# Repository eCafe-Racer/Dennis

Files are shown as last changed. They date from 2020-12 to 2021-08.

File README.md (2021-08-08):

# Dennis

Dennis is a part of the eCafe Racer project, a collaboration between Tim
LaGreca, Jordyn Brosemer, and Connor Winiarczyk where we are attempting to
build an electric racing motorcycle for fun and street cred.

The board serve's as both a controller for the bike's 12V digital signals
(such as its turn signals and brake lights), and also as a general interface
to the bike's CAN bus. We plan to use this interface both during development
for things like data acquisition and validation testing, as well as in the 
final product in order to provide features like control over bluetooth and
diagnostics.

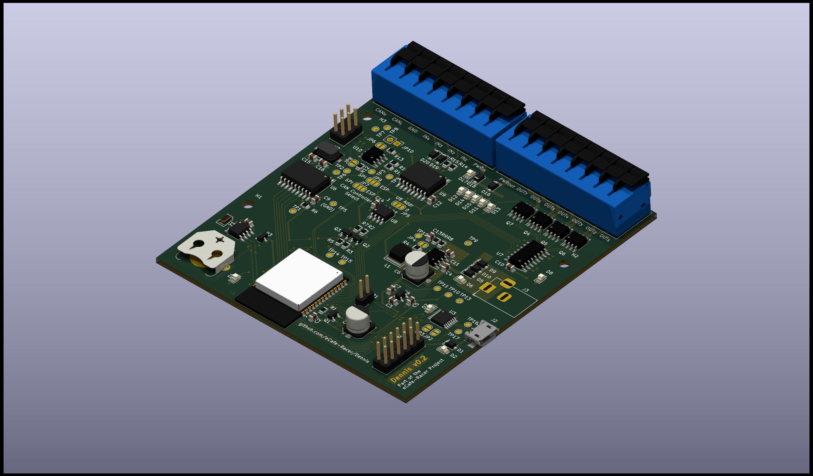
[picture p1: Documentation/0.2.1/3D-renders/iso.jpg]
Isometric View


## Design 

Dennis was originally designed as a carrier board for the Raspberry Pi
[Compute Module 4](https://www.raspberrypi.org/products/compute-module-4/?variant=raspberry-pi-cm4001000),
which aimed to integrate a complete embedded Linux system with the rest of the
circuitry, with peripherals controlled directly by the Pi's GPIO pins.
There were a number of issues with this approach, not the least of which was
that, as hobbyists, we lacked the equipment required to reliably solder the
CM4's high density connectors. There were some more subtle issues as well,
including that the high level of integration made our design much more
difficult to modify, and that the need to include integrated communication
interfaces for the pi increased both the size of the board and its complexity.

Our solution was simply to remove the Compute Module from the design, replacing
it with an ESP32 microcontroller. The microcontroller will be able to perform 
some simple logical control over the board, but its main job will be to provide
an interface to the board's peripherals over UART or USB, allowing a more
powerful computer to connect and perform higher level control and more
sophisticated analysis.  

In order to make interfacing with external computers easier, a 12 pin connector
(J1) was added to Dennis that exactly matches the pinout of the first 12
pins of the 40 pin connector on a traditional Raspberry Pi board. This allows
a Raspberry Pi to be mounted adjacent to Dennis in whatever enclosure it is 
being used in, and with a single ribbon cable, connect to the ESP's UART
interface, as well as the strapping pins needed to do firmware updates, the
board's I2C bus, and 5V power supply. These signals can also be controlled
over USB by way of an MCP2221A, giving us the flexibility to use other external
computers as well.

## Peripherals

Dennis has a 12V GPIO system with 7 digital outputs and 4 digital inputs.
Digital outputs can be set to either 12V (on), or High Impedance (off), meaning
they cannot sink current. The digital inputs consist of two "signal" inputs,
which measure voltage, and two "switch" inputs, which measure resistance to
ground. The switch inputs are meant to make it easier to install switches or
buttons on the bike and to program them for near arbitrary behavior, like
turn signals or a horn.

## Resources

- [Schematic](https://raw.githubusercontent.com/eCafe-Racer/Dennis/master/Documentation/0.2.1/schematic.pdf)
- [Step File](https://raw.githubusercontent.com/eCafe-Racer/Dennis/master/Documentation/0.2.1/step-file.step)
- [Gerbers](https://raw.githubusercontent.com/eCafe-Racer/Dennis/master/production/0.2/gerbers.zip)

- Top View
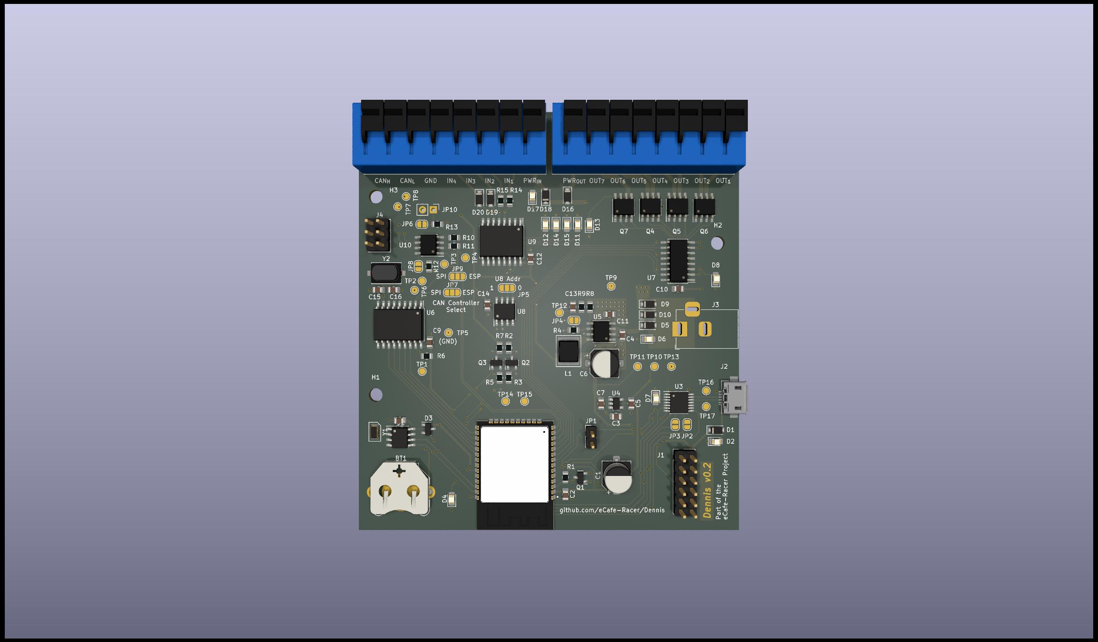
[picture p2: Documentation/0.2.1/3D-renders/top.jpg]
Top View


- Bottom View
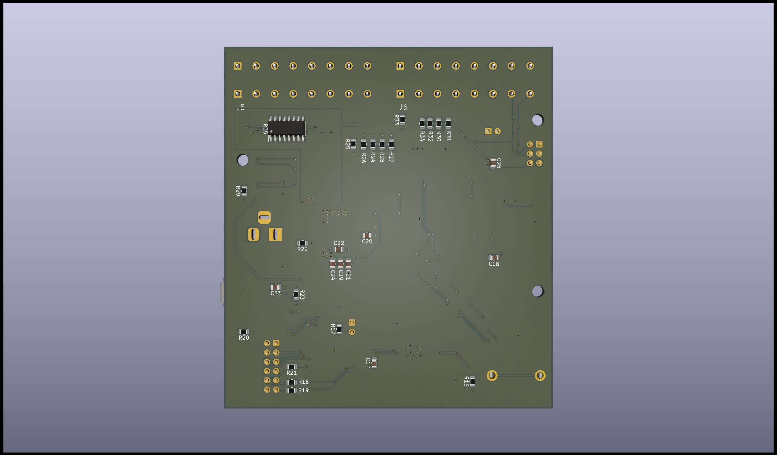
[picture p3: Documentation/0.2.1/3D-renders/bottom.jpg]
Bottom View


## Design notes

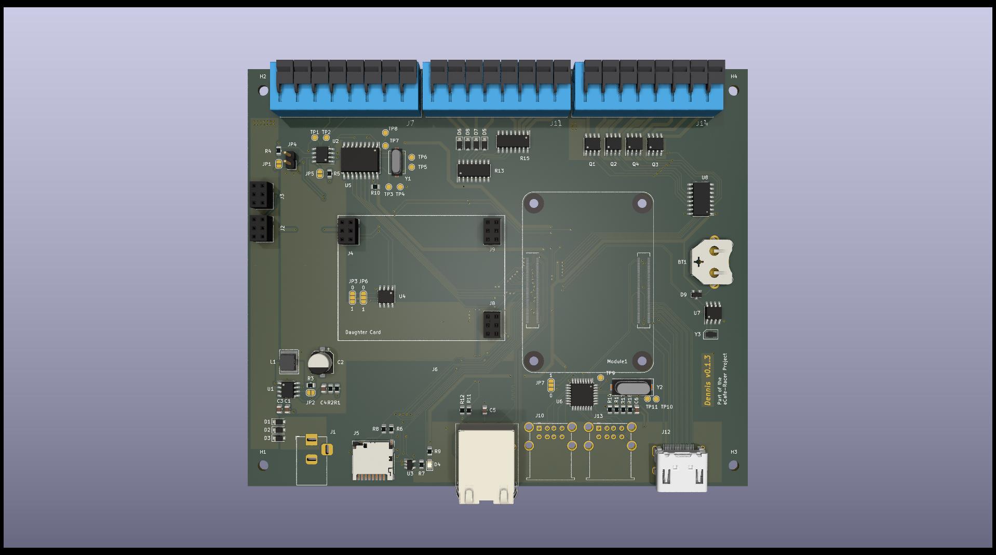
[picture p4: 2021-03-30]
Documentation/0.1.3/images/render_front.jpg

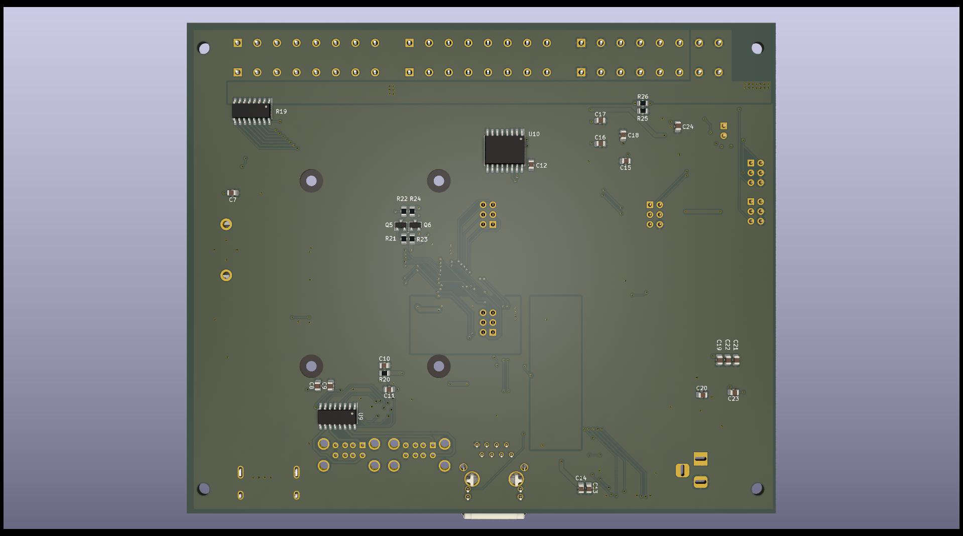
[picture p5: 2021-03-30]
Documentation/0.1.3/images/render_back.jpg

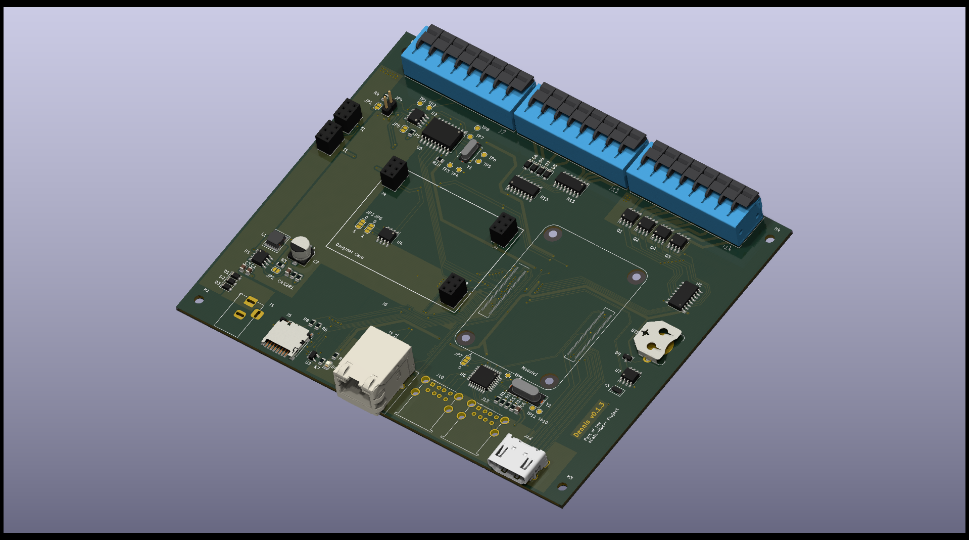
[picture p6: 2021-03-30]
Documentation/0.1.3/images/render_iso.png

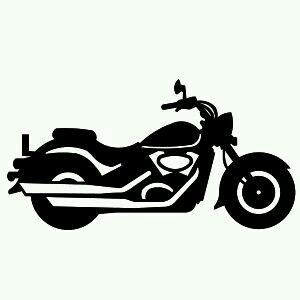
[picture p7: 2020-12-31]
page_layout/cafe-racer-art.jpg

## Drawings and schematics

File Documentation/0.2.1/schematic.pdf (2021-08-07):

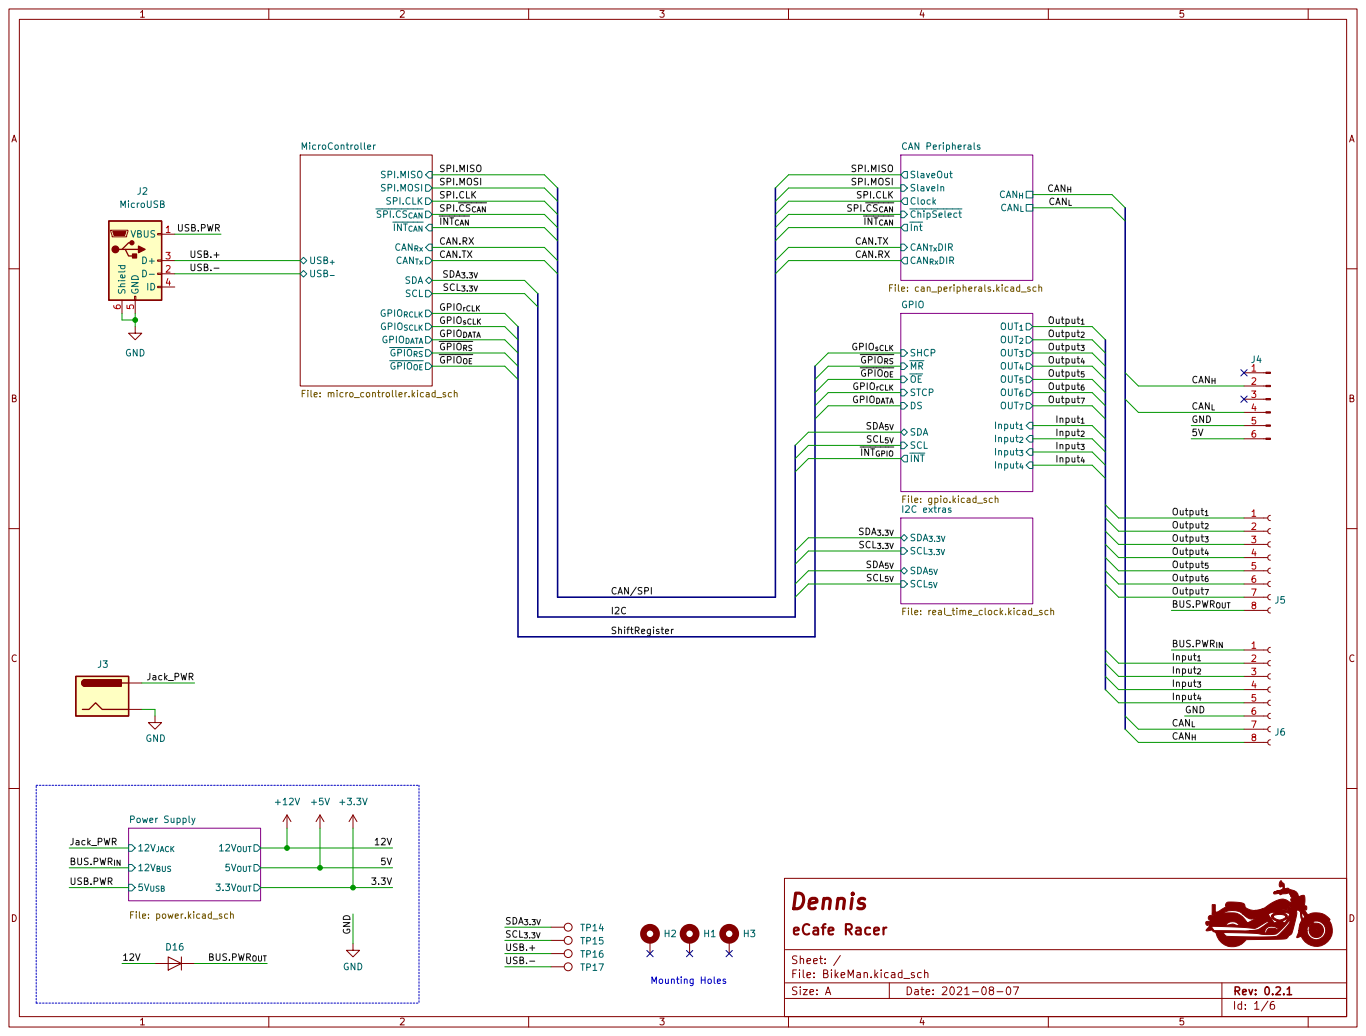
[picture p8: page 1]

MicroController File: micro_controller.kicad_sch SPI.MISO
SCL_{3.3V} SPI.MISO
SPI.MOSI SPI.CLK GPIO_{DATA}
GPIO_{sCLK} USB.+ SCL_{3.3V}
~{GPIO_{RS}} 5V
~{GPIO_{RS}}

SPI.MOSI SPI.MISO

File: can_peripherals.kicad_sch SlaveOut SlaveIn ~{Int}

SPI.MOSI SPI.CLK

SPI.~{CS_{CAN}} CAN.RX CAN.TX GND
~{SPI.CS_{CAN}}
~{INT_{CAN}}
CAN_{Rx}
CAN_{Tx}
~{GPIO_{OE}} SDA

SCL_{3.3V} CAN.RX CAN.TX

BUS.PWR_{IN} USB.PWR

Id: 1/6 Dennis
File: BikeMan.kicad_sch Sheet: / eCafe Racer

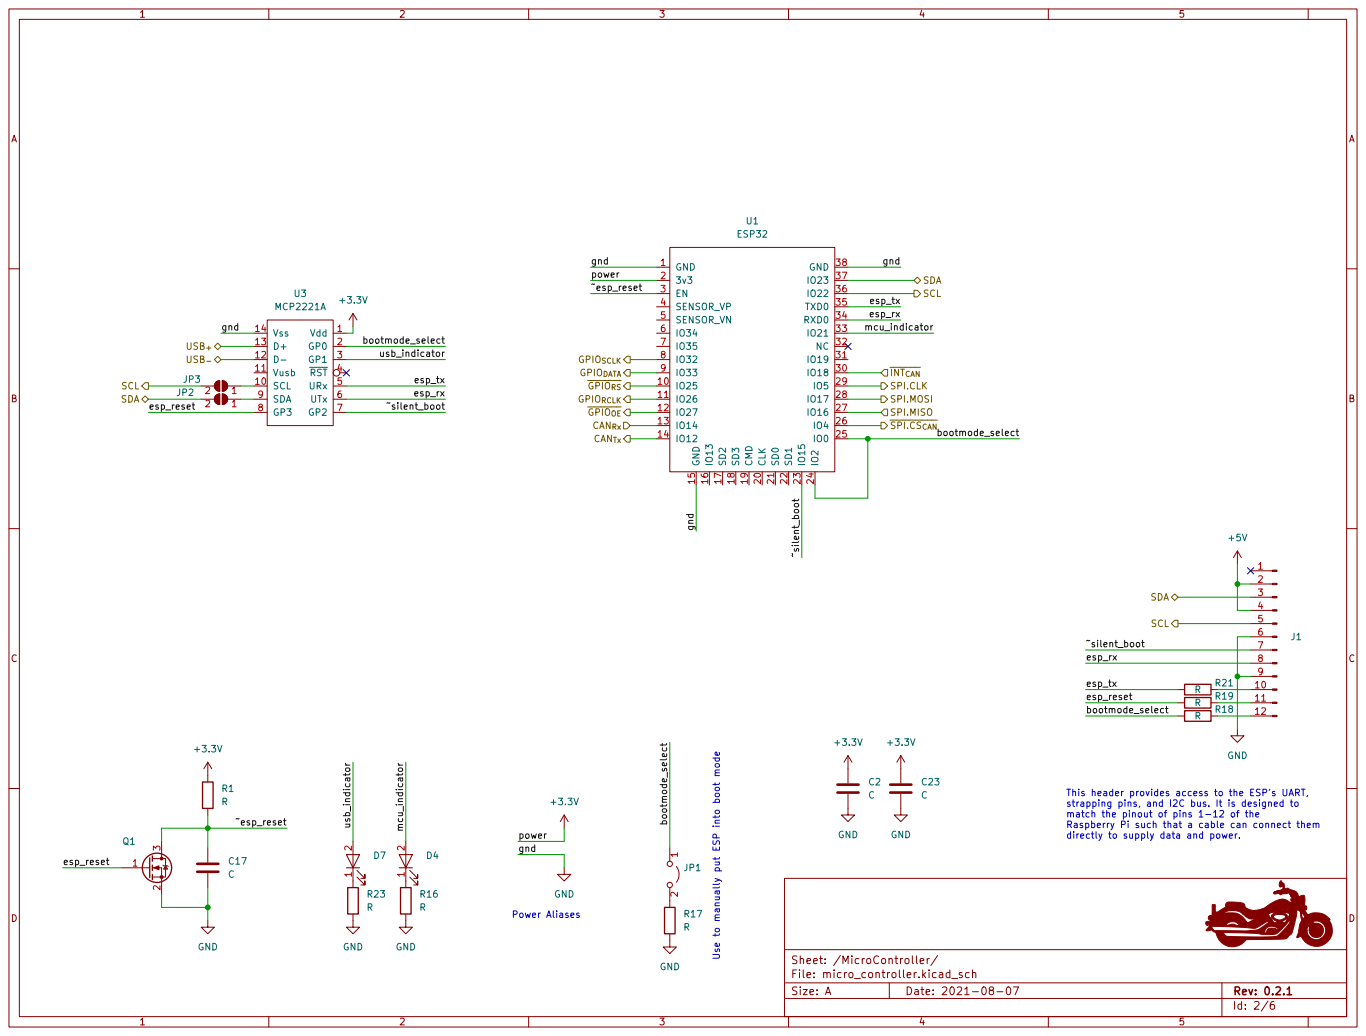
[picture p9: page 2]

strapping pins, and I2C bus. It is designed to
match the pinout of pins 1-12 of the
Raspberry Pi such that a cable can connect them
directly to supply data and power.

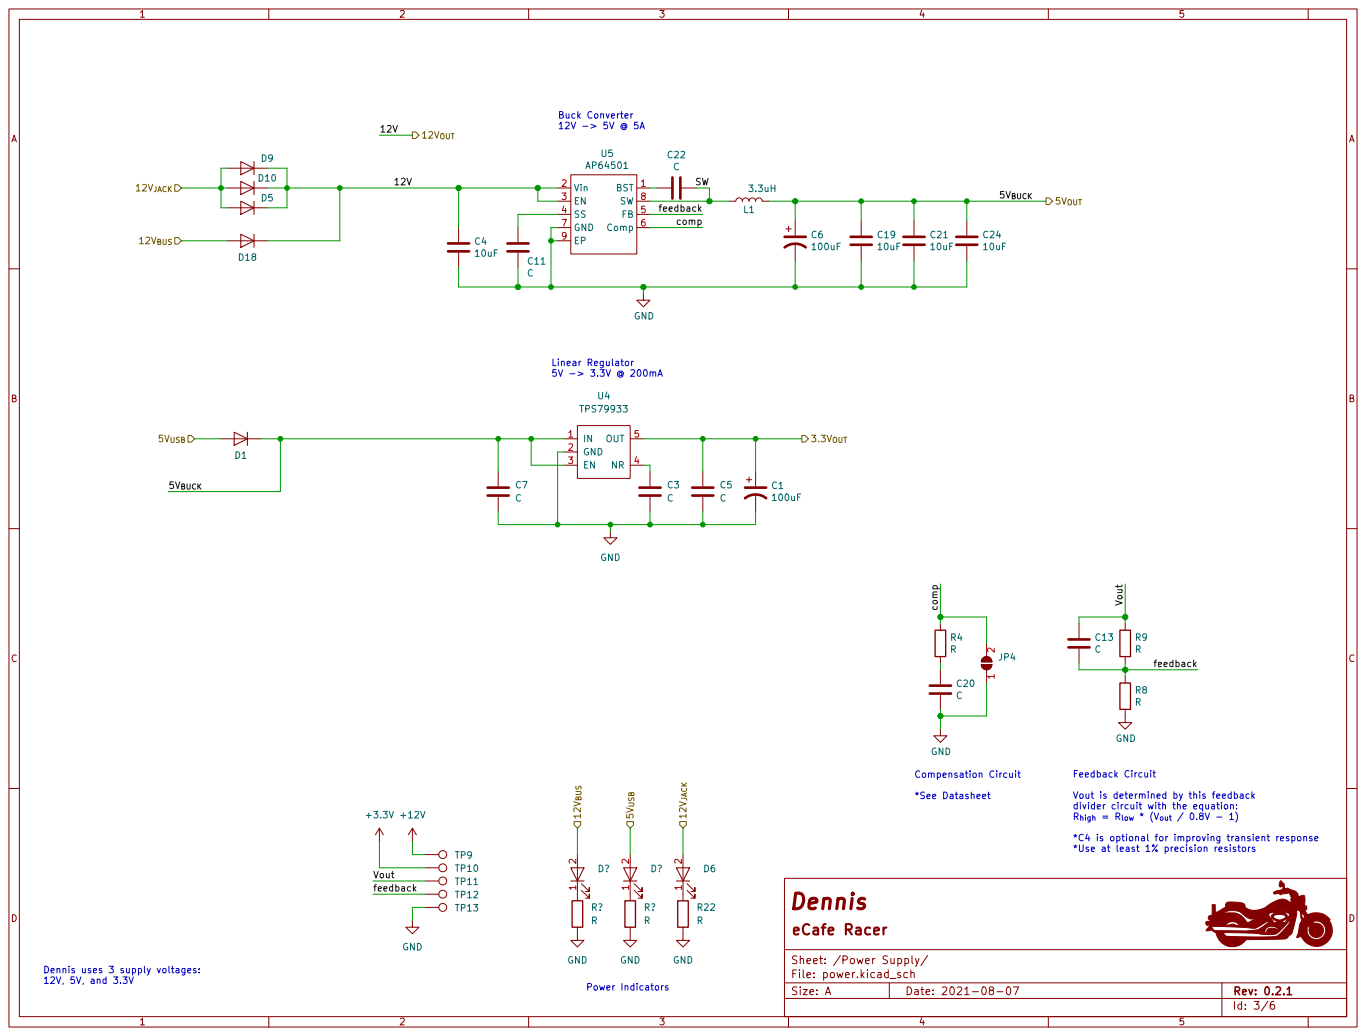
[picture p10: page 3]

Feedback Circuit Vout is determined by this feedback

divider circuit with the equation:
R_{high} = R_{low} * (V_{out} / 0.8V - 1)

*C4 is optional for improving transient response
*Use at least 1% precision resistors

Dennis uses 3 supply voltages: 12V, 5V, and 3.3V

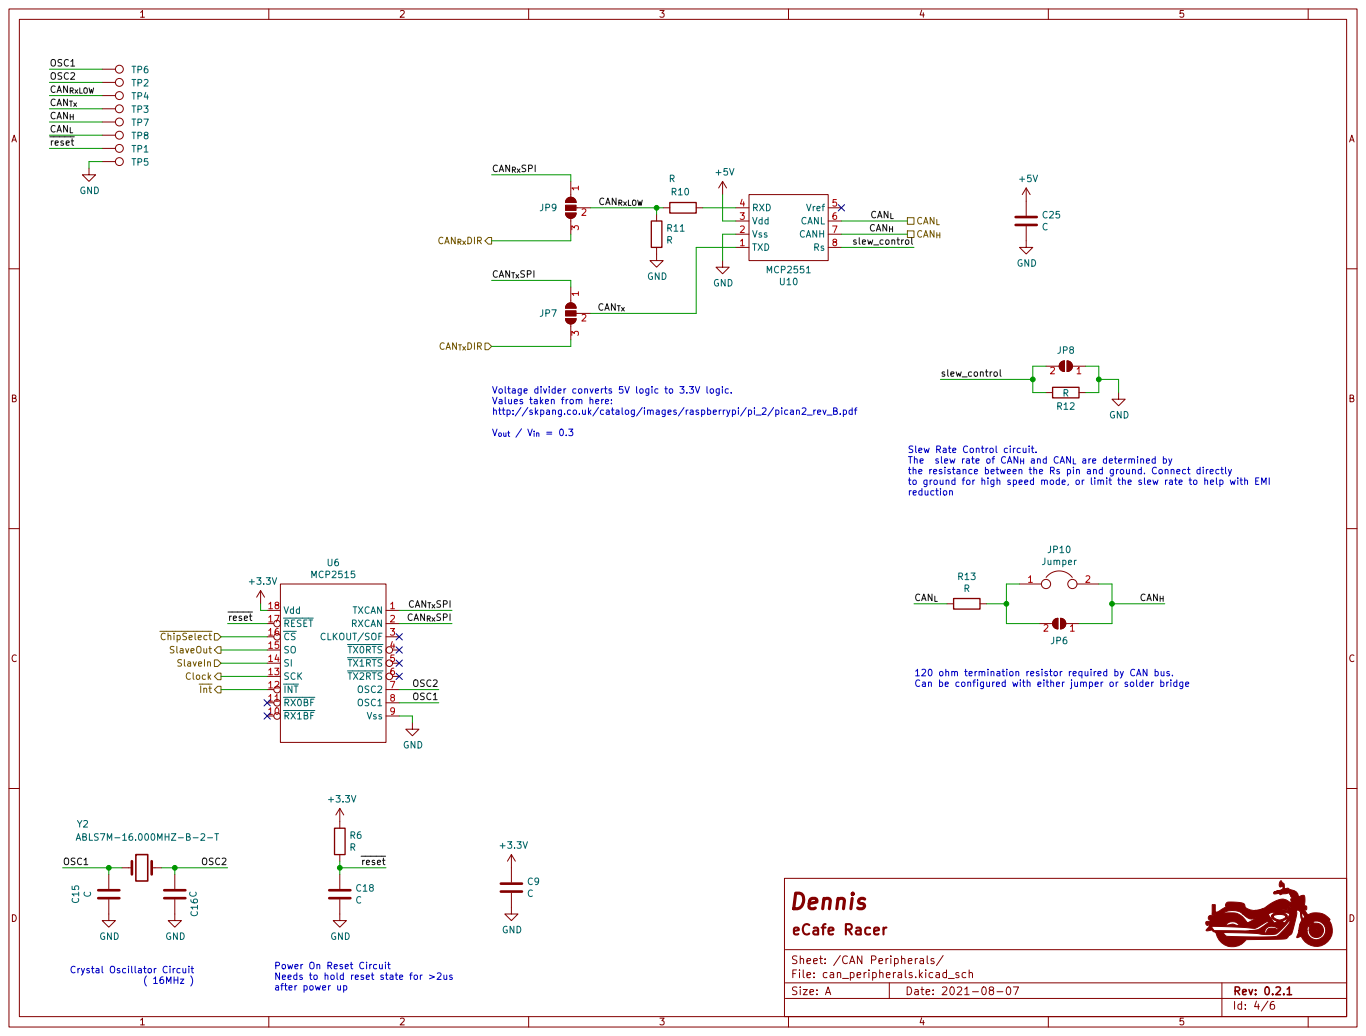
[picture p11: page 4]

Voltage divider converts 5V logic to 3.3V logic. Values taken from here: http://skpang.co.uk/catalog/images/raspberrypi/pi_2/pican2_rev_B.pdf

Slew Rate Control circuit. The slew rate of CAN_{H} and CAN_{L} are determined by

to ground for high speed mode, or limit the slew rate to help with EMI reduction Power On Reset Circuit Needs to hold reset state for >2us after power up

the resistance between the Rs pin and ground. Connect directly

~{ChipSelect}
~{Int} Clock SlaveIn SlaveOut

120 ohm termination resistor required by CAN bus.
Can be configured with either jumper or solder bridge

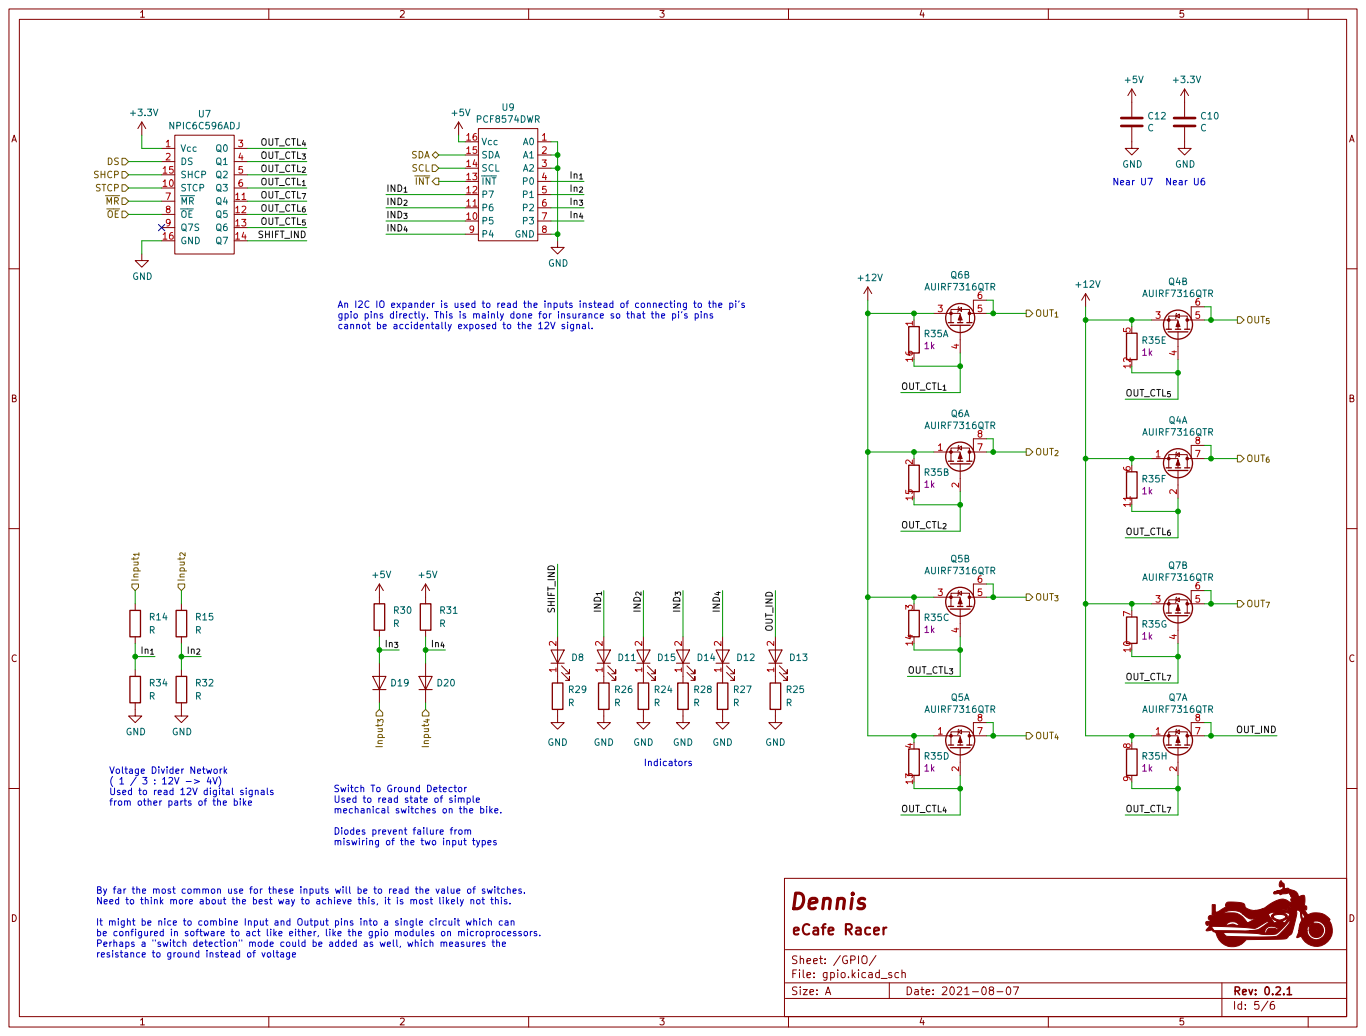
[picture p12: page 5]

1k SCL ~{MR} STCP
Near U7 Voltage Divider Network

An I2C IO expander is used to read the inputs instead of connecting to the pi's
gpio pins directly. This is mainly done for insurance so that the pi's pins

Indicators Switch To Ground Detector Used to read state of simple mechanical switches on the bike. Diodes prevent failure from

Used to read 12V digital signals
from other parts of the bike

miswiring of the two input types

By far the most common use for these inputs will be to read the value of switches.
Need to think more about the best way to achieve this, it is most likely not this.

Id: 5/6 Dennis
File: gpio.kicad_sch Sheet: /GPIO/ eCafe Racer

It might be nice to combine Input and Output pins into a single circuit which can
be configured in software to act like either, like the gpio modules on microprocessors.
Perhaps a "switch detection" mode could be added as well, which measures the
resistance to ground instead of voltage

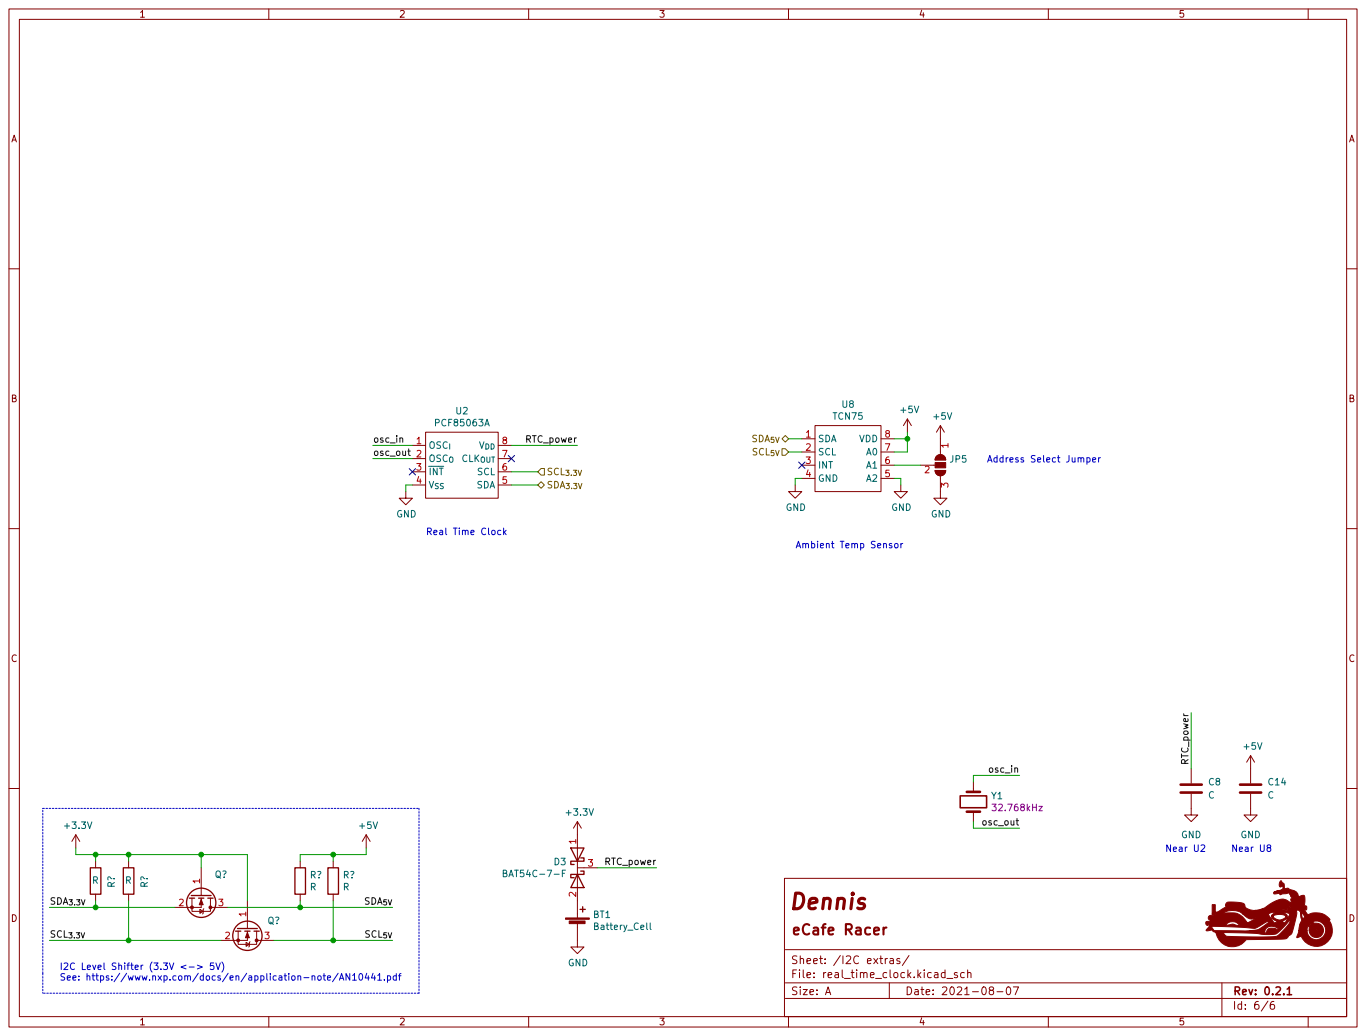
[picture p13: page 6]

File: real_time_clock.kicad_sch Sheet: /I2C extras/ eCafe Racer GND

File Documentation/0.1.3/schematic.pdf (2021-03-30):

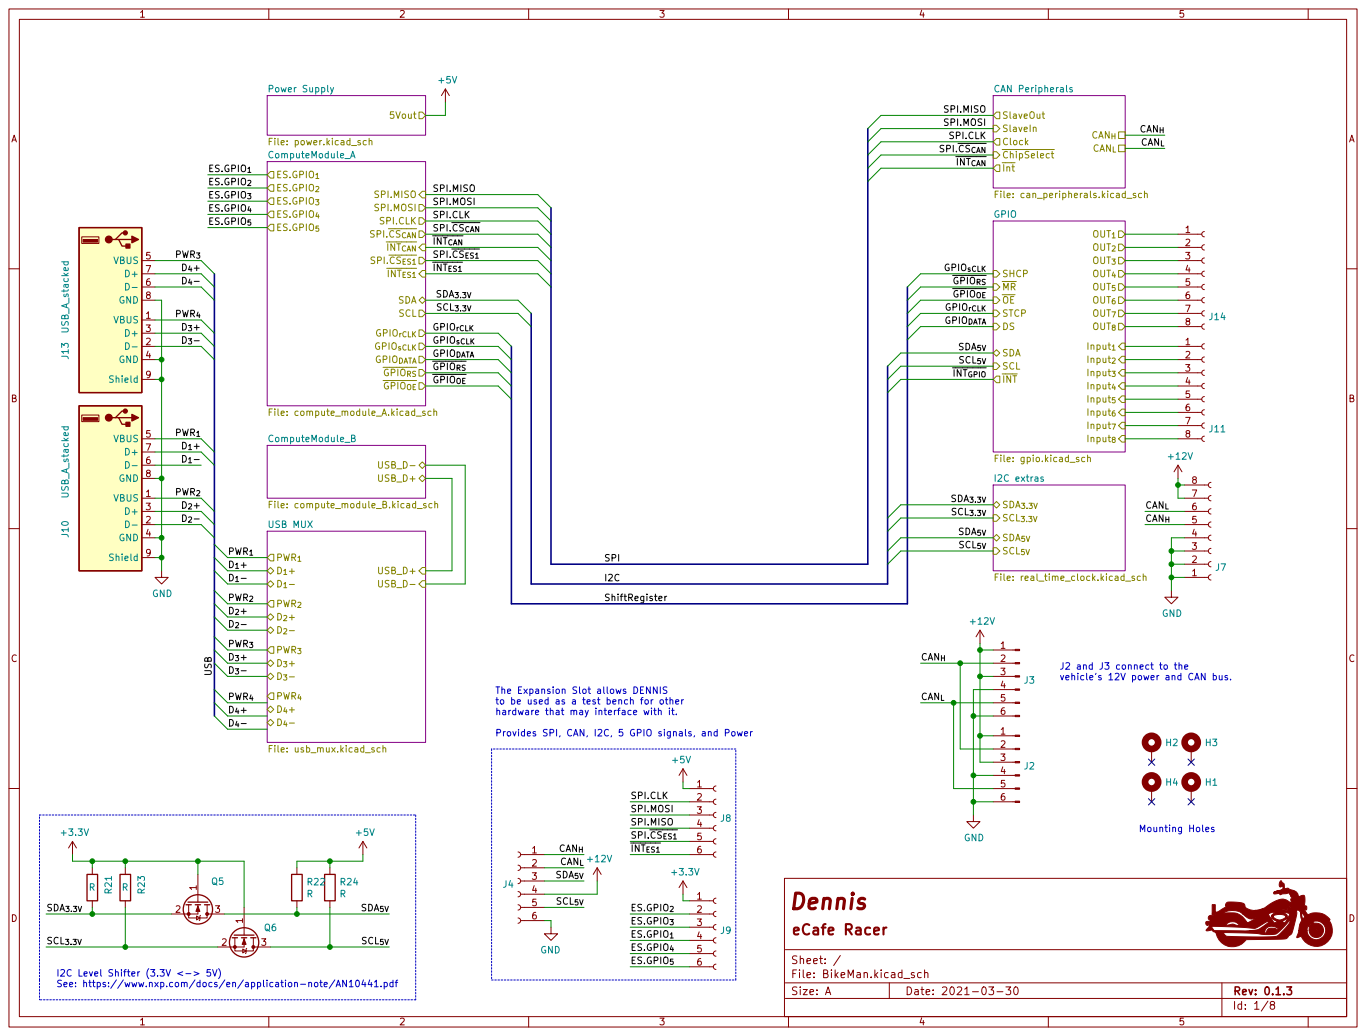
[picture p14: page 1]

SPI.MOSI SPI.MISO

SPI.~CS_{CAN} SPI.MISO
SPI.MOSI SPI.CLK

File: BikeMan.kicad_sch Sheet: / eCafe Racer USB MUX

SPI.MOSI ShiftRegister SPI

vehicle's 12V power and CAN bus.

The Expansion Slot allows DENNIS
to be used as a test bench for other hardware that may interface with it.

Provides SPI, CAN, I2C, 5 GPIO signals, and Power

I2C Level Shifter (3.3V <-> 5V)
See: https://www.nxp.com/docs/en/application-note/AN10441.pdf

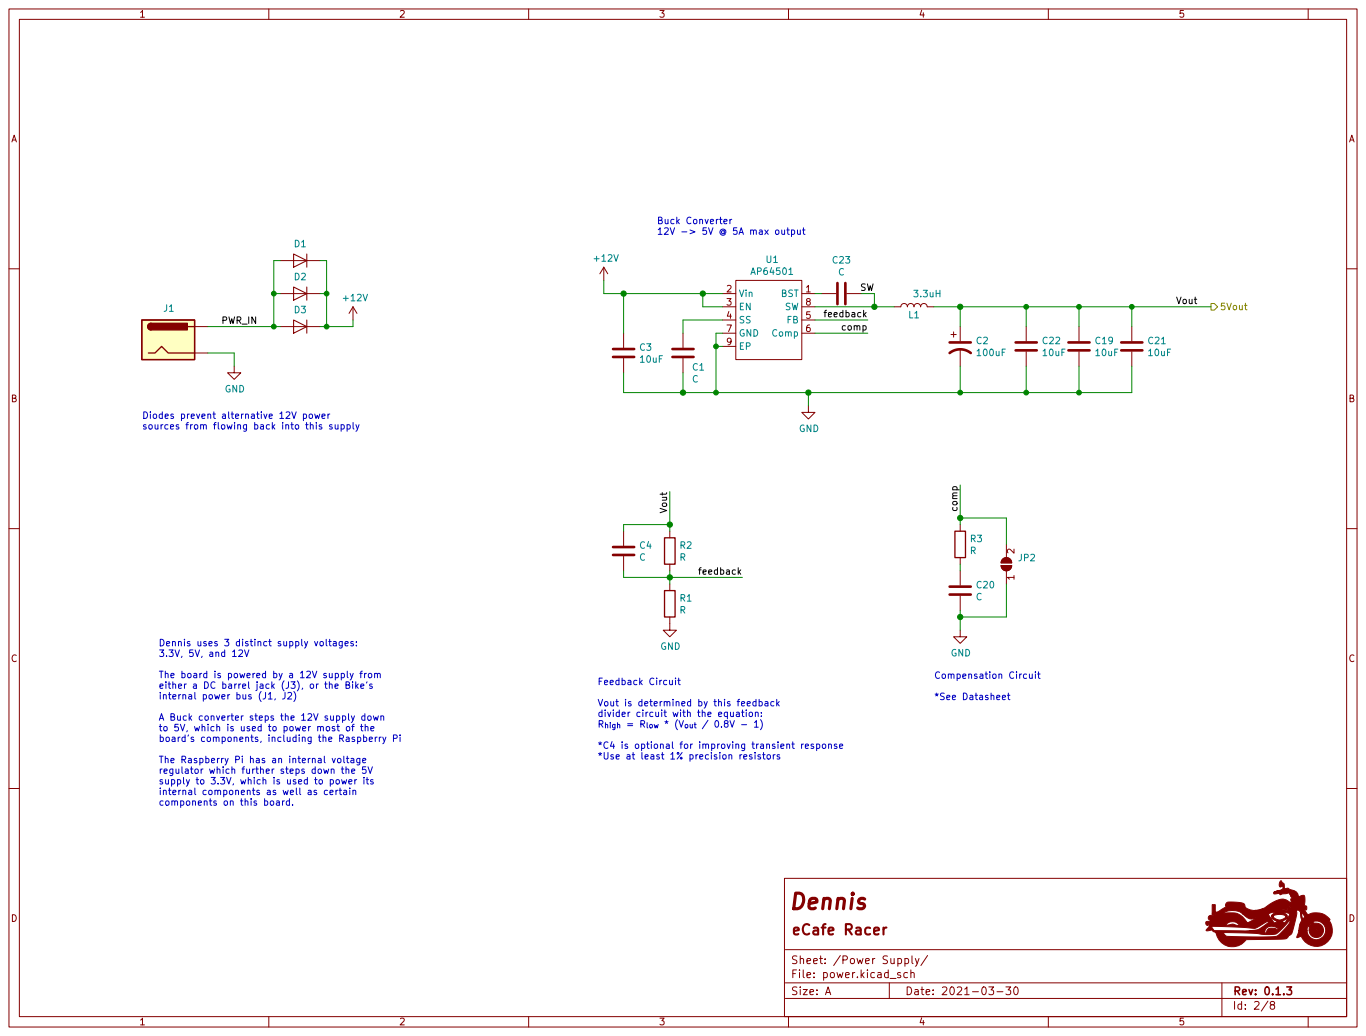
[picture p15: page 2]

Buck Converter 12V -> 5V @ 5A max output

Diodes prevent alternative 12V power
sources from flowing back into this supply

Dennis uses 3 distinct supply voltages: 3.3V, 5V, and 12V

The board is powered by a 12V supply from
either a DC barrel jack (J3), or the Bike's
internal power bus (J1, J2)

Compensation Circuit *See Datasheet

A Buck converter steps the 12V supply down
to 5V, which is used to power most of the
board's components, including the Raspberry Pi

divider circuit with the equation:
R_{high} = R_{low} * (V_{out} / 0.8V - 1)

*C4 is optional for improving transient response
*Use at least 1% precision resistors

The Raspberry Pi has an internal voltage
regulator which further steps down the 5V
supply to 3.3V, which is used to power its
internal components as well as certain

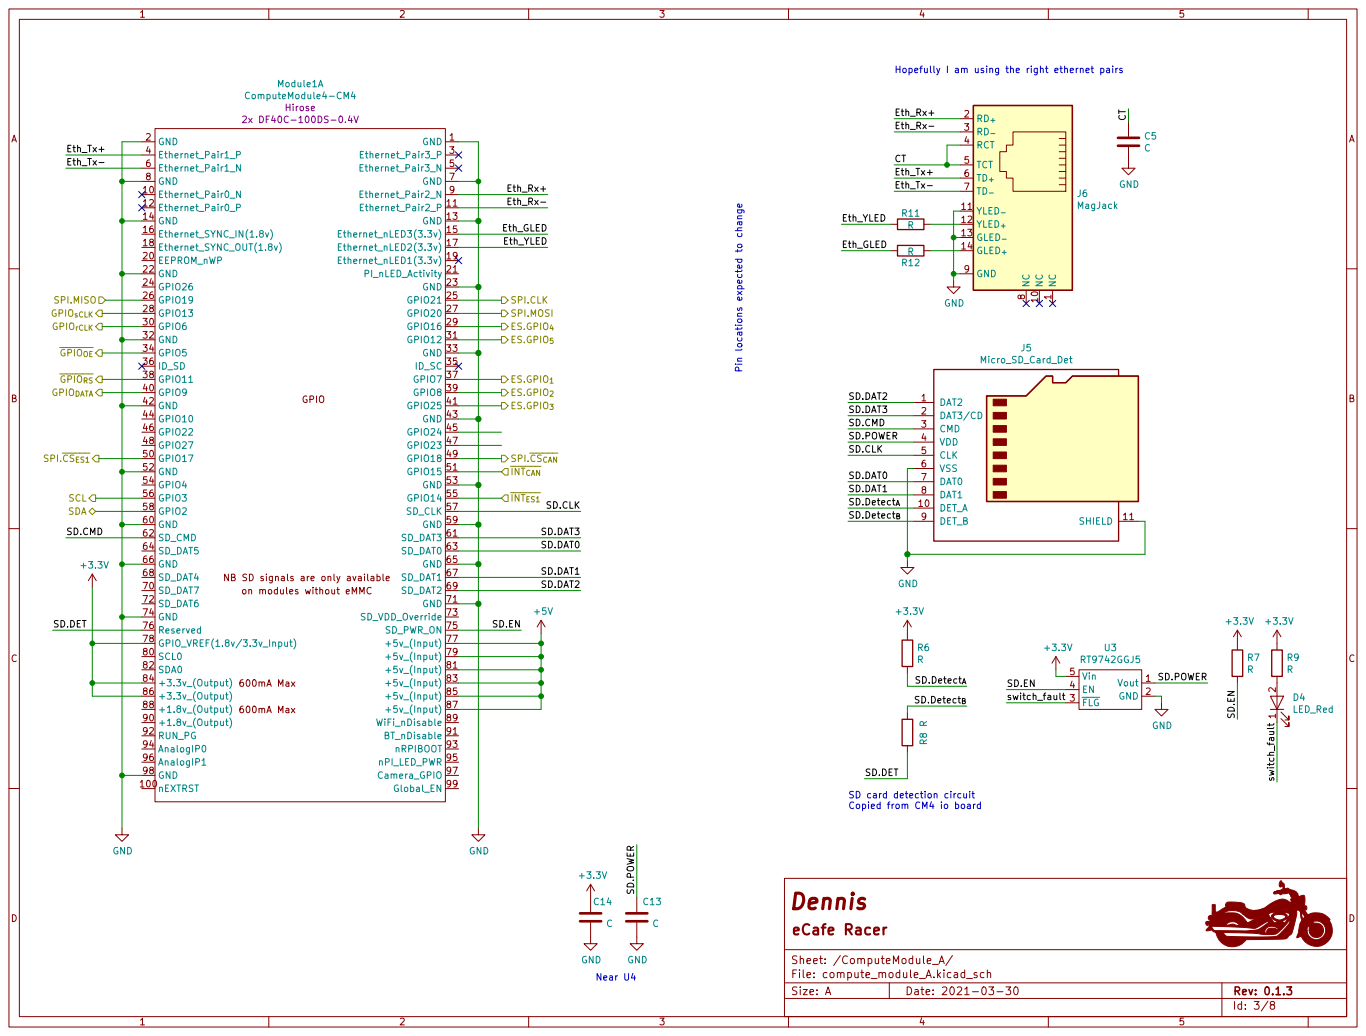
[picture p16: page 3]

Hopefully I am using the right ethernet pairs
J6MagJack R8 R
SD.Detect_{B} Eth_YLED
ES.GPIO_{4} SPI.MOSI ~INT_{ES1}

Eth_Tx+ Eth_Tx- SD.DAT0 SD.DAT3 SD.CLK
ES.GPIO_{2} Eth_Rx- Eth_YLED

SD.DAT2 SD.DAT3 SD.CMD

600mA Max 600mA Max NB SD signals are only available

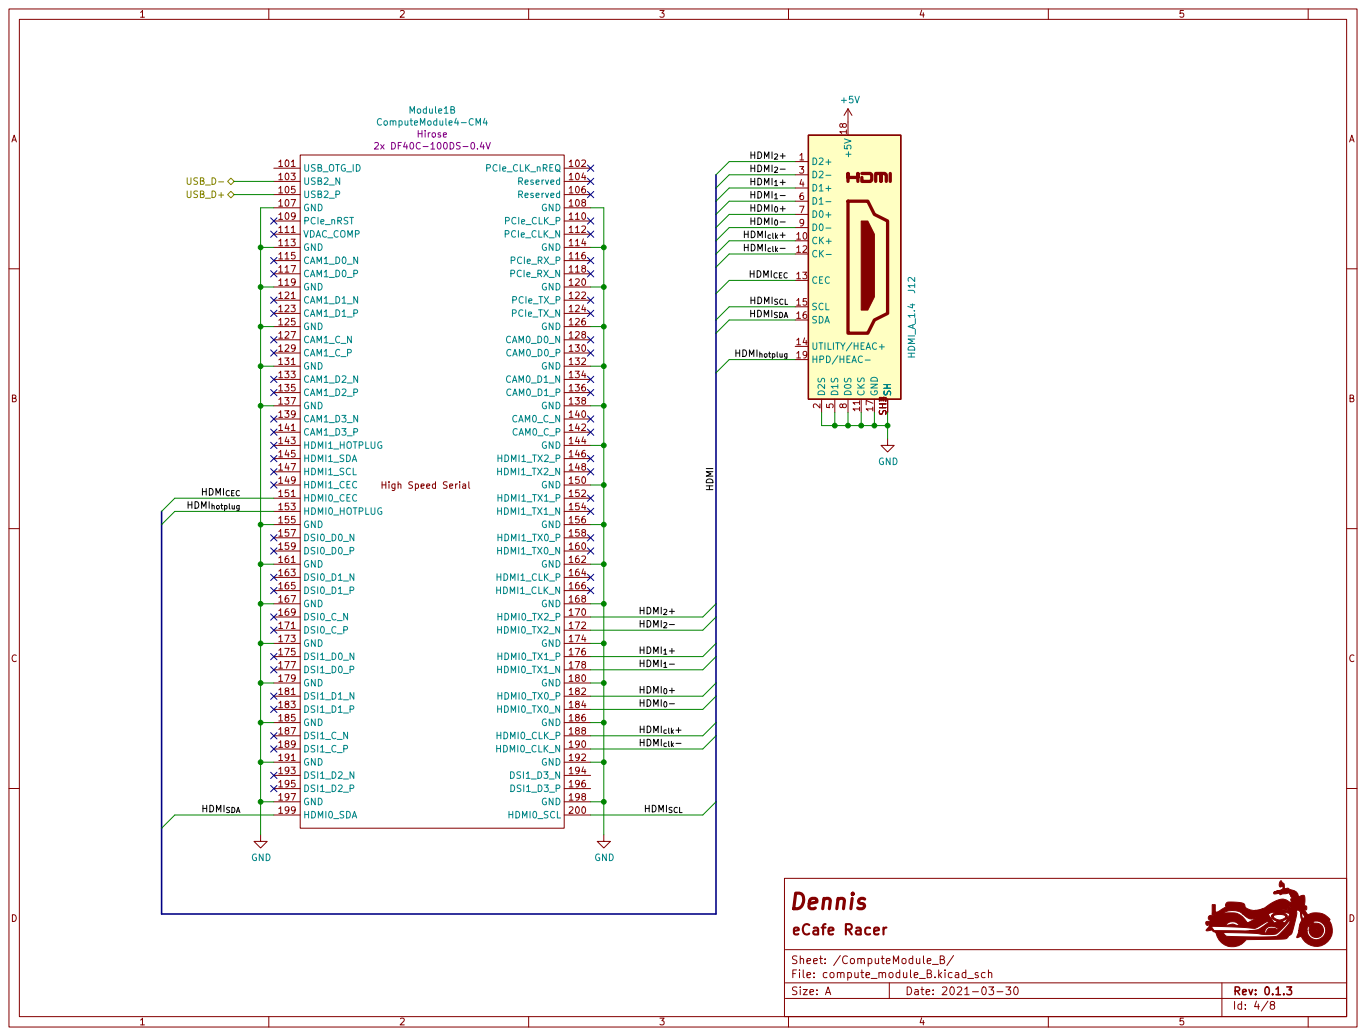
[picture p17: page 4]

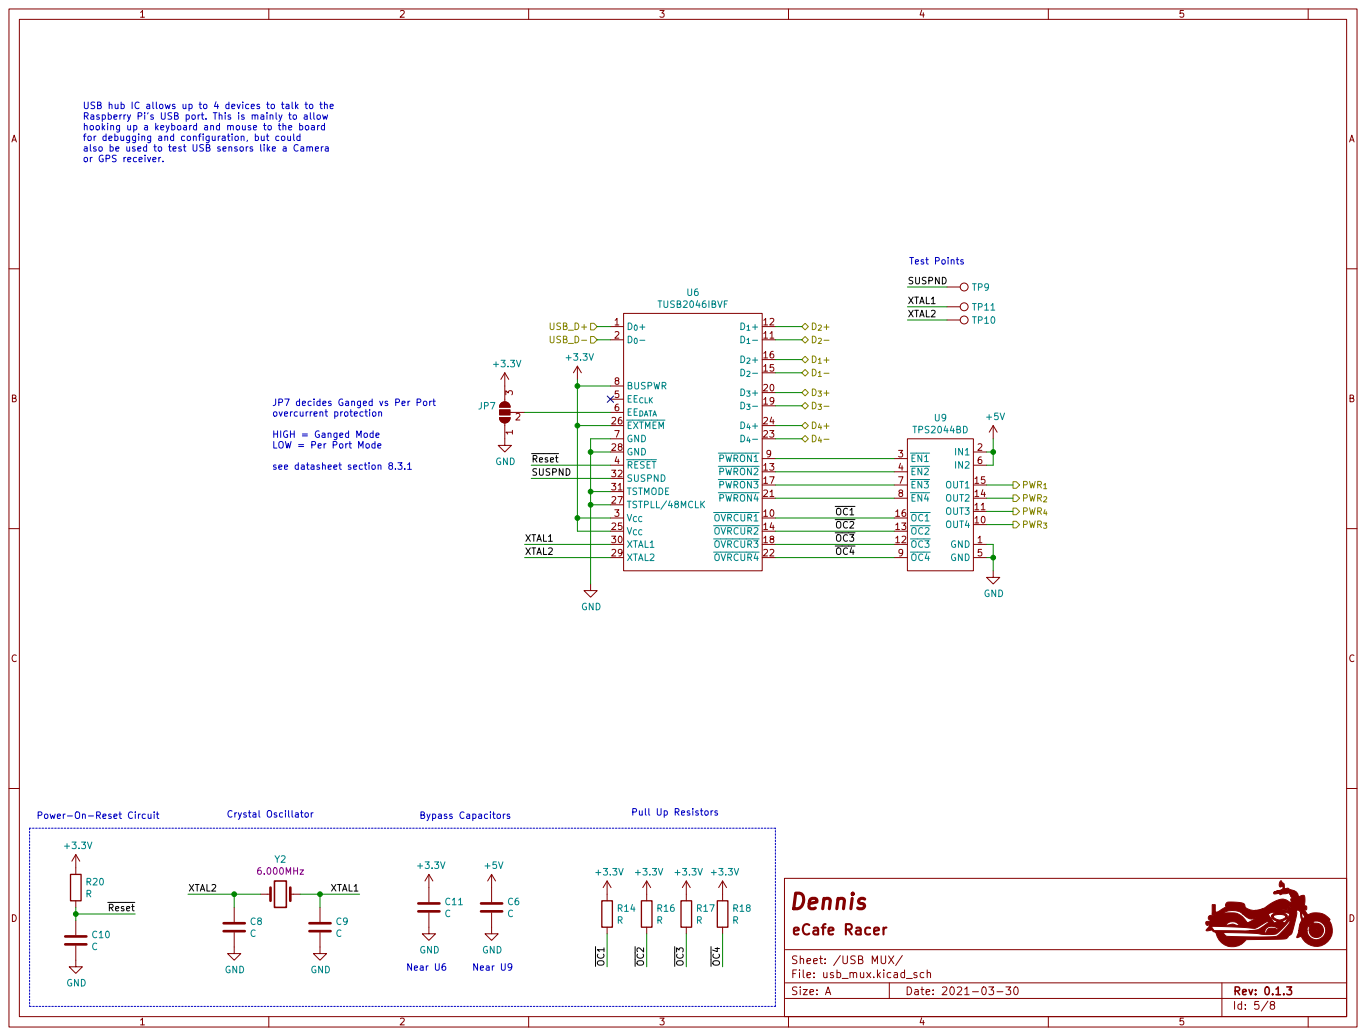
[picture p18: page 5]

USB hub IC allows up to 4 devices to talk to the
Raspberry Pi's USB port. This is mainly to allow
hooking up a keyboard and mouse to the board
for debugging and configuration, but could
also be used to test USB sensors like a Camera
+3.3VR17 R GND

HIGH = Ganged Mode
LOW = Per Port Mode

File: usb_mux.kicad_sch Sheet: /USB MUX/ eCafe Racer C9 C

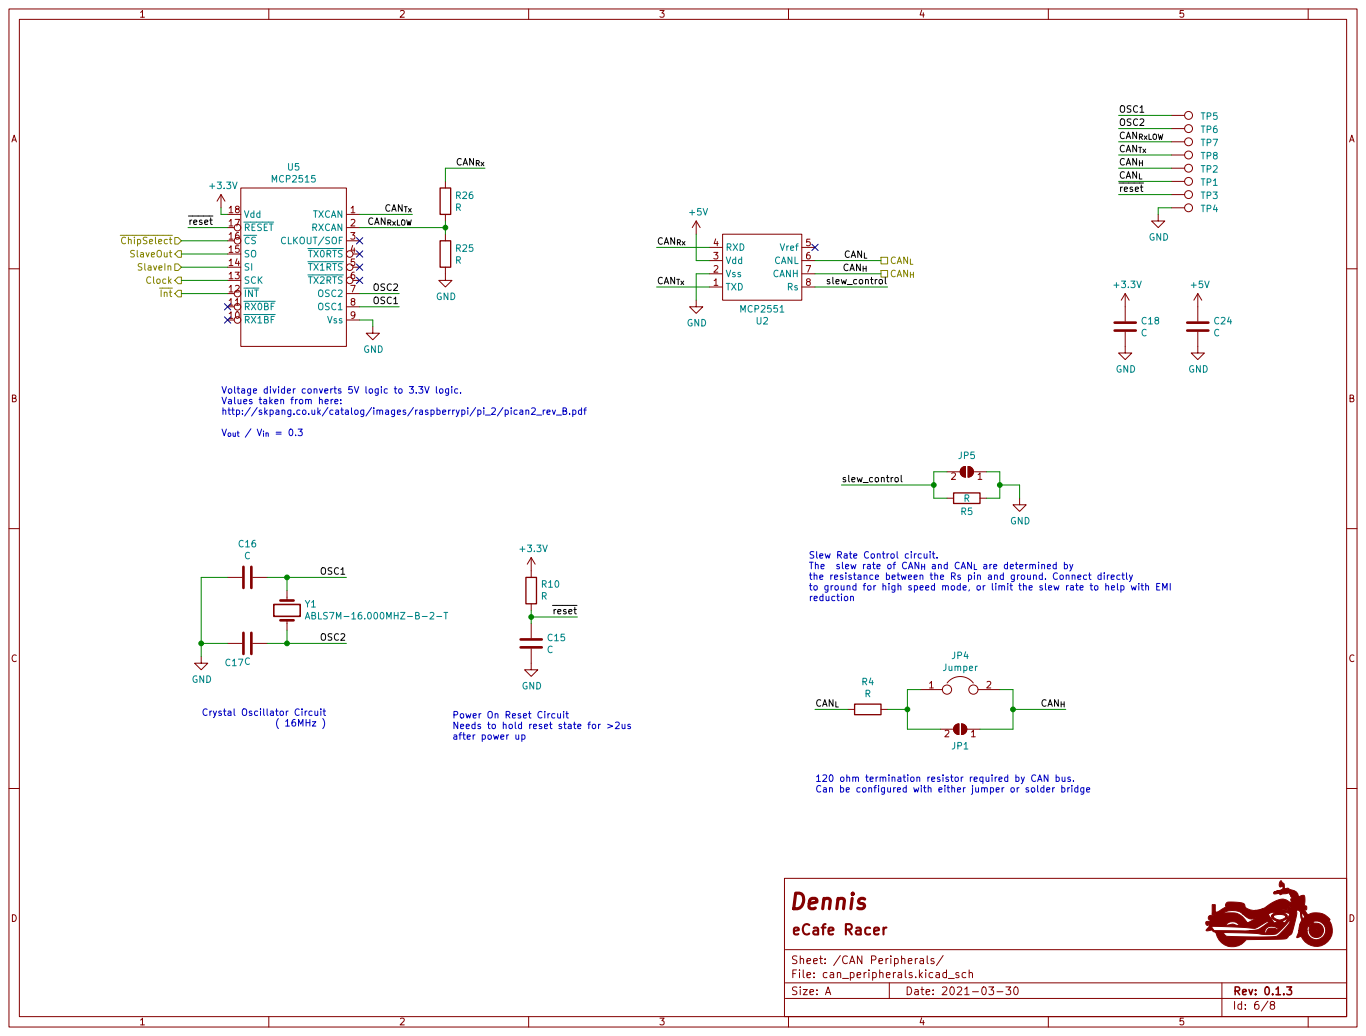
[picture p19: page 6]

CAN_{Tx} OSC2 Crystal Oscillator Circuit

Voltage divider converts 5V logic to 3.3V logic. Values taken from here: http://skpang.co.uk/catalog/images/raspberrypi/pi_2/pican2_rev_B.pdf

Can be configured with either jumper or solder bridge Slew Rate Control circuit. The slew rate of CAN_{H} and CAN_{L} are determined by

the resistance between the Rs pin and ground. Connect directly
to ground for high speed mode, or limit the slew rate to help with EMI reduction

120 ohm termination resistor required by CAN bus.


Near U6 Voltage Divider Network

Near U7 By far the most common use for these inputs will be to read the value of switches.

An I2C IO expander is used to read the inputs instead of connecting to the pi's
gpio pins directly. This is mainly done for insurance so that the pi's pins
cannot be accidentally exposed to the 12V signal.

OUT_CTL_{8} Switch To Ground Detector Used to read state of simple mechanical switches on the bike. Diodes prevent failure from

Used to read 12V digital signals
from other parts of the bike

miswiring of the two input types

Need to think more about the best way to achieve this, it is most likely not this.

It might be nice to combine Input and Output pins into a single circuit which can
be configured in software to act like either, like the gpio modules on microprocessors.
Perhaps a "switch detection" mode could be added as well, which measures the
resistance to ground instead of voltage

File: gpio.kicad_sch Sheet: /GPIO/ eCafe Racer


Id: 8/8 Dennis
File: real_time_clock.kicad_sch Sheet: /I2C extras/ eCafe Racer

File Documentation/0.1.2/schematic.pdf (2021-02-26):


SPI.~CS_{CAN} SPI.MISO
SPI.MOSI SPI.CLK
~GPIO_{RS} SPI.CLK

The Expansion Slot allows DENNIS
to be used as a test bench for other hardware that may interface with it.

Id: 1/7 Dennis
File: BikeMan.kicad_sch Sheet: / eCafe Racer

Provides SPI, CAN, I2C, 5 GPIO signals, and Power


Hopefully I am using the right ethernet pairs
Eth_Tx_{+} SD.DAT3 Eth_Rx_{+}

SD.power SD.CMD

SPI.MOSI SPI.MISO

SD.DAT1 SD.DAT0 SD.CLK

~INT_{CAN} SDA
SD.DET SD.CMD

SD.DAT0 SD.DAT3 SD.CLK

600mA Max 600mA Max NB SD signals are only available


TODO: make of find footprint
HDMI_{clk}+ HDMI

TODO: figure out these signals

USB hub IC allows up to 4 devices to talk to the Pi's USB port.
This is mainly to allow hooking up a keyboard and mouse to the board
for debugging and configuration, and will most likely not be a part of the board
when it becomes a product.


Buck Converter 12V -> 5V @ 5A max output

CM4 board uses 4 (10uF) ceramic and 1 (100uF)
electrolytic capacitors in parallel

( See Datasheet ) TODO:
- Bus power input (From DC to DC converter in battery
- Bus power delivery

Vout is determined by this feedback divider circuit
through the equation: R_{high} = R_{low} * (V_{out} / 0.8V - 1)

Use at least 1% precision resistors Feedback Circuit

Id: 4/7 Dennis
File: power.kicad_sch Sheet: /Power/ eCafe Racer


slew_control Power On Reset Circuit Needs to hold reset state for >2us after power up

the resistance between the Rs pin and ground. Connect directly
to ground for high speed mode, or limit the slew rate to help with EMI reduction

120 ohm termination resistor required by CAN bus.
Can be configured with either jumper or solder bridge


An I2C IO expander is used to read the inputs instead of connecting to the pi's
gpio pins directly. This is mainly done for insurance so that the pi's pins
cannot be accidentally exposed to the 12V signal.

Voltage Divider Network
Used to read 12V digital signals
from other parts of the bike

miswiring of the two input types

By far the most common use for these inputs will be to read the value of switches.
Need to think more about the best way to achieve this, it is most likely not this.

It might be nice to combine Input and Output pins into a single circuit which can
be configured in software to act like either, like the gpio modules on microprocessors.
Perhaps a "switch detection" mode could be added as well, which measures the

Id: 6/7 Dennis
File: gpio.kicad_sch Sheet: /GPIO/ eCafe Racer


2GND
File: real_time_clock.kicad_sch Sheet: /RealTimeClock/ eCafe Racer BT1 Battery_Cell

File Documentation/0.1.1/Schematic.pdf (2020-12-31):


TODO: connect to pi

Four USB ports is probably overkill

Id: 1/7 Dennis
File: BikeMan.kicad_sch Sheet: / eCafe Racer


the resistance between the Rs pin and ground. Connect directly
to ground for high speed mode, or limit the slew rate to help with EMI reduction

Can be configured with either jumper or solder bridge


CM4 board uses 4 (10uF) ceramic and 1 (100uF)
electrolytic capacitors in parallel

Feedback Circuit Vout is determined by this feedback divider circuit
through the equation: R_{high} = R_{low} * (V_{out} / 0.8V - 1)

Optional capacitor can improve transient response

File: power.kicad_sch Sheet: /Power/ eCafe Racer GND


Thinking more and more that ethernet and
power over ethernet might be worth it.

Would be helpful mainly if we want to install this in a server rack as
part of a dyno-room style electrical testing stand

5 GPIO pins are used to drive a shift register
controlling output on the board's 12V GPIO module.

TODO: select gpio pins to use

600mA Max 600mA Max NB SD signals are only available


An I2C IO expander is used to read the inputs instead of connecting to the pi's
gpio pins directly. This is mainly done for insurance so that the pi's pins
cannot be accidentally exposed to the 12V signal.

Voltage Divider Network (12V -> 5V)
Used to read 12V digital input signals from other parts of the bike
Use integrated resistor network if possible (TODO: spec)

By far the most common use for these inputs will be to read the value of switches.
Need to think more about the best way to achieve this, it is most likely not this.

It might be nice to combine Input and Output pins into a single circuit which can
be configured in software to act like either, like the gpio modules on microprocessors.
Perhaps a "switch detection" mode could be added as well, which measures the
resistance to ground instead of voltage


File: real_time_clock.kicad_sch Sheet: /RealTimeClock/ eCafe Racer BT1


TODO: figure out these signals

USB hub IC allows up to 4 devices to talk to the Pi's USB port.
This is mainly to allow hooking up a keyboard and mouse to the board
for debugging and configuration, and will most likely not be a part of the board
when it becomes a product.

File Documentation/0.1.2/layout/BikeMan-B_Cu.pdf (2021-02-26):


Id: 1/1 Dennis
File: BikeMan.kicad_pcb Sheet: eCafe Racer

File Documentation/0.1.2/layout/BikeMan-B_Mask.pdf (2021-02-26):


Id: 1/1 Dennis
File: BikeMan.kicad_pcb Sheet: eCafe Racer

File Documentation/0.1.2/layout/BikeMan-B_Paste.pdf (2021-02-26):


Id: 1/1 Dennis
File: BikeMan.kicad_pcb Sheet: eCafe Racer

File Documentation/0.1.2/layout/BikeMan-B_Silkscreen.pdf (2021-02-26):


Id: 1/1 Dennis
File: BikeMan.kicad_pcb Sheet: eCafe Racer

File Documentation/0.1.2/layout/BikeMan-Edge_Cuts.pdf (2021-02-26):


Id: 1/1 Dennis
File: BikeMan.kicad_pcb Sheet: eCafe Racer

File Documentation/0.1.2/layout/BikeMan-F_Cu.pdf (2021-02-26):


Id: 1/1 Dennis
File: BikeMan.kicad_pcb Sheet: eCafe Racer



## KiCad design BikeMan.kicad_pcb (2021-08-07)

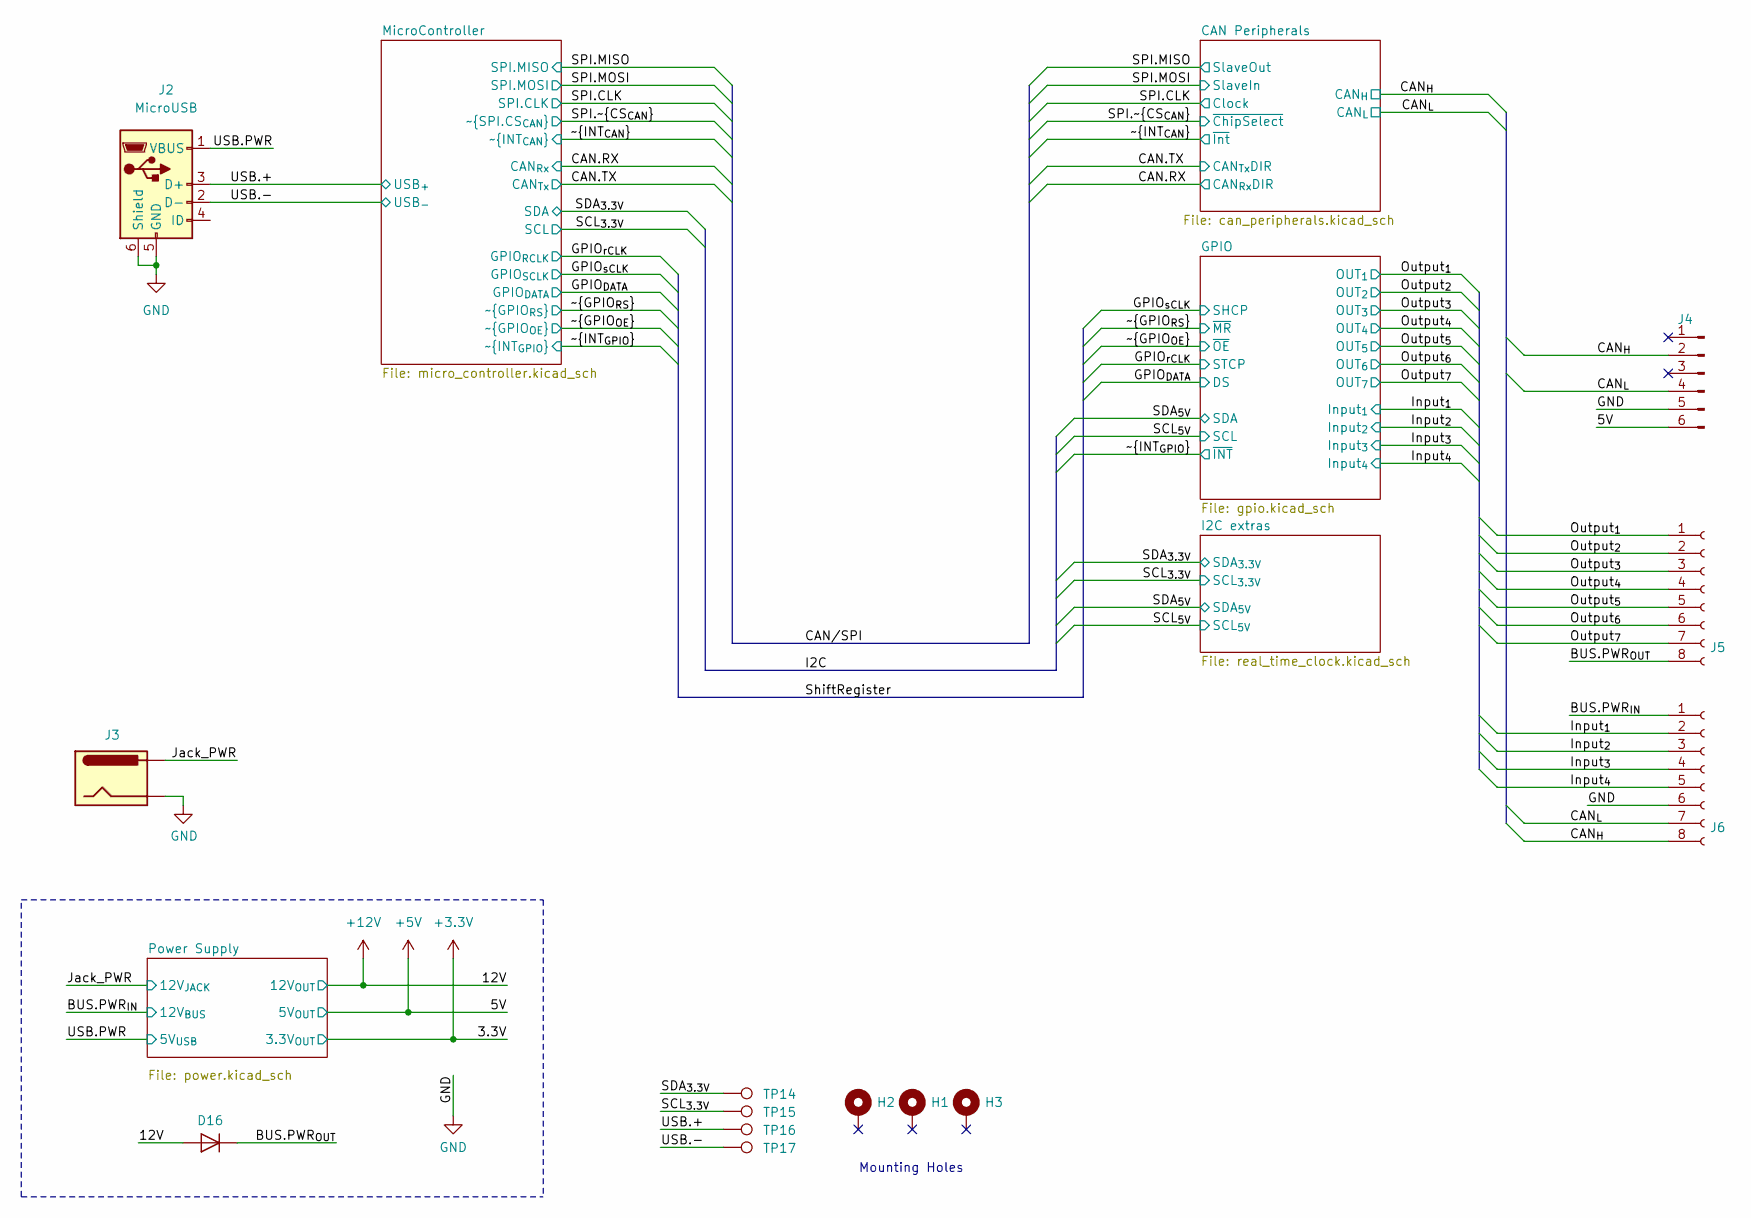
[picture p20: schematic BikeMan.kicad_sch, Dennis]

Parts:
D16: Diode; D_SOD-123F; Manufacturer Part NHP220SFT3G
H1, H2, H3: MountingHole_Pad; MountingHole_3.2mm_M3
J2: MicroUSB; USB_Micro-B_Amphenol_10104110_Horizontal; Manufacture Part 10118192-0002LF
J3: Barrel_Jack; BarrelJack_Horizontal; Manufacuturer Part 4840.2201
J4: Conn_01x06_Male; PinHeader_2x03_P2.54mm_Vertical
J5, J6: PushConnector_8pos; CUI_TBL004-508-08BE-2BE; Manufacturer Part TBL004-508-08BE-2GY
TP14, TP15, TP16, TP17: TestPoint; TestPoint_Pad_D1.5mm

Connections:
+5V: J4.6; also elsewhere on the board
+12V: D16.2 (A); also elsewhere on the board
/BUS.PWR_{IN}: J6.1; also elsewhere on the board
/BUS.PWR_{OUT}: D16.1 (K), J5.8
/CAN_{H}: J4.2, J6.8; also elsewhere on the board
/CAN_{L}: J4.4, J6.7; also elsewhere on the board
/Input_{1}: J6.2; also elsewhere on the board
/Input_{2}: J6.3; also elsewhere on the board
/Input_{3}: J6.4; also elsewhere on the board
/Input_{4}: J6.5; also elsewhere on the board
/Jack_PWR: J3.1; also elsewhere on the board
/Output_{1}: J5.1; also elsewhere on the board
/Output_{2}: J5.2; also elsewhere on the board
/Output_{3}: J5.3; also elsewhere on the board
/Output_{4}: J5.4; also elsewhere on the board
/Output_{5}: J5.5; also elsewhere on the board
/Output_{6}: J5.6; also elsewhere on the board
/Output_{7}: J5.7; also elsewhere on the board
/SCL_{3.3V}: TP15.1; also elsewhere on the board
/SDA_{3.3V}: TP14.1; also elsewhere on the board
/USB.+: J2.3 (D+), TP16.1; also elsewhere on the board
/USB.-: J2.2 (D-), TP17.1; also elsewhere on the board
/USB.PWR: J2.1 (VBUS); also elsewhere on the board
GND: J2.5 (GND), J2.6 (Shield), J3.2, J4.5, J6.6; also elsewhere on the board

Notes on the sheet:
Mounting Holes

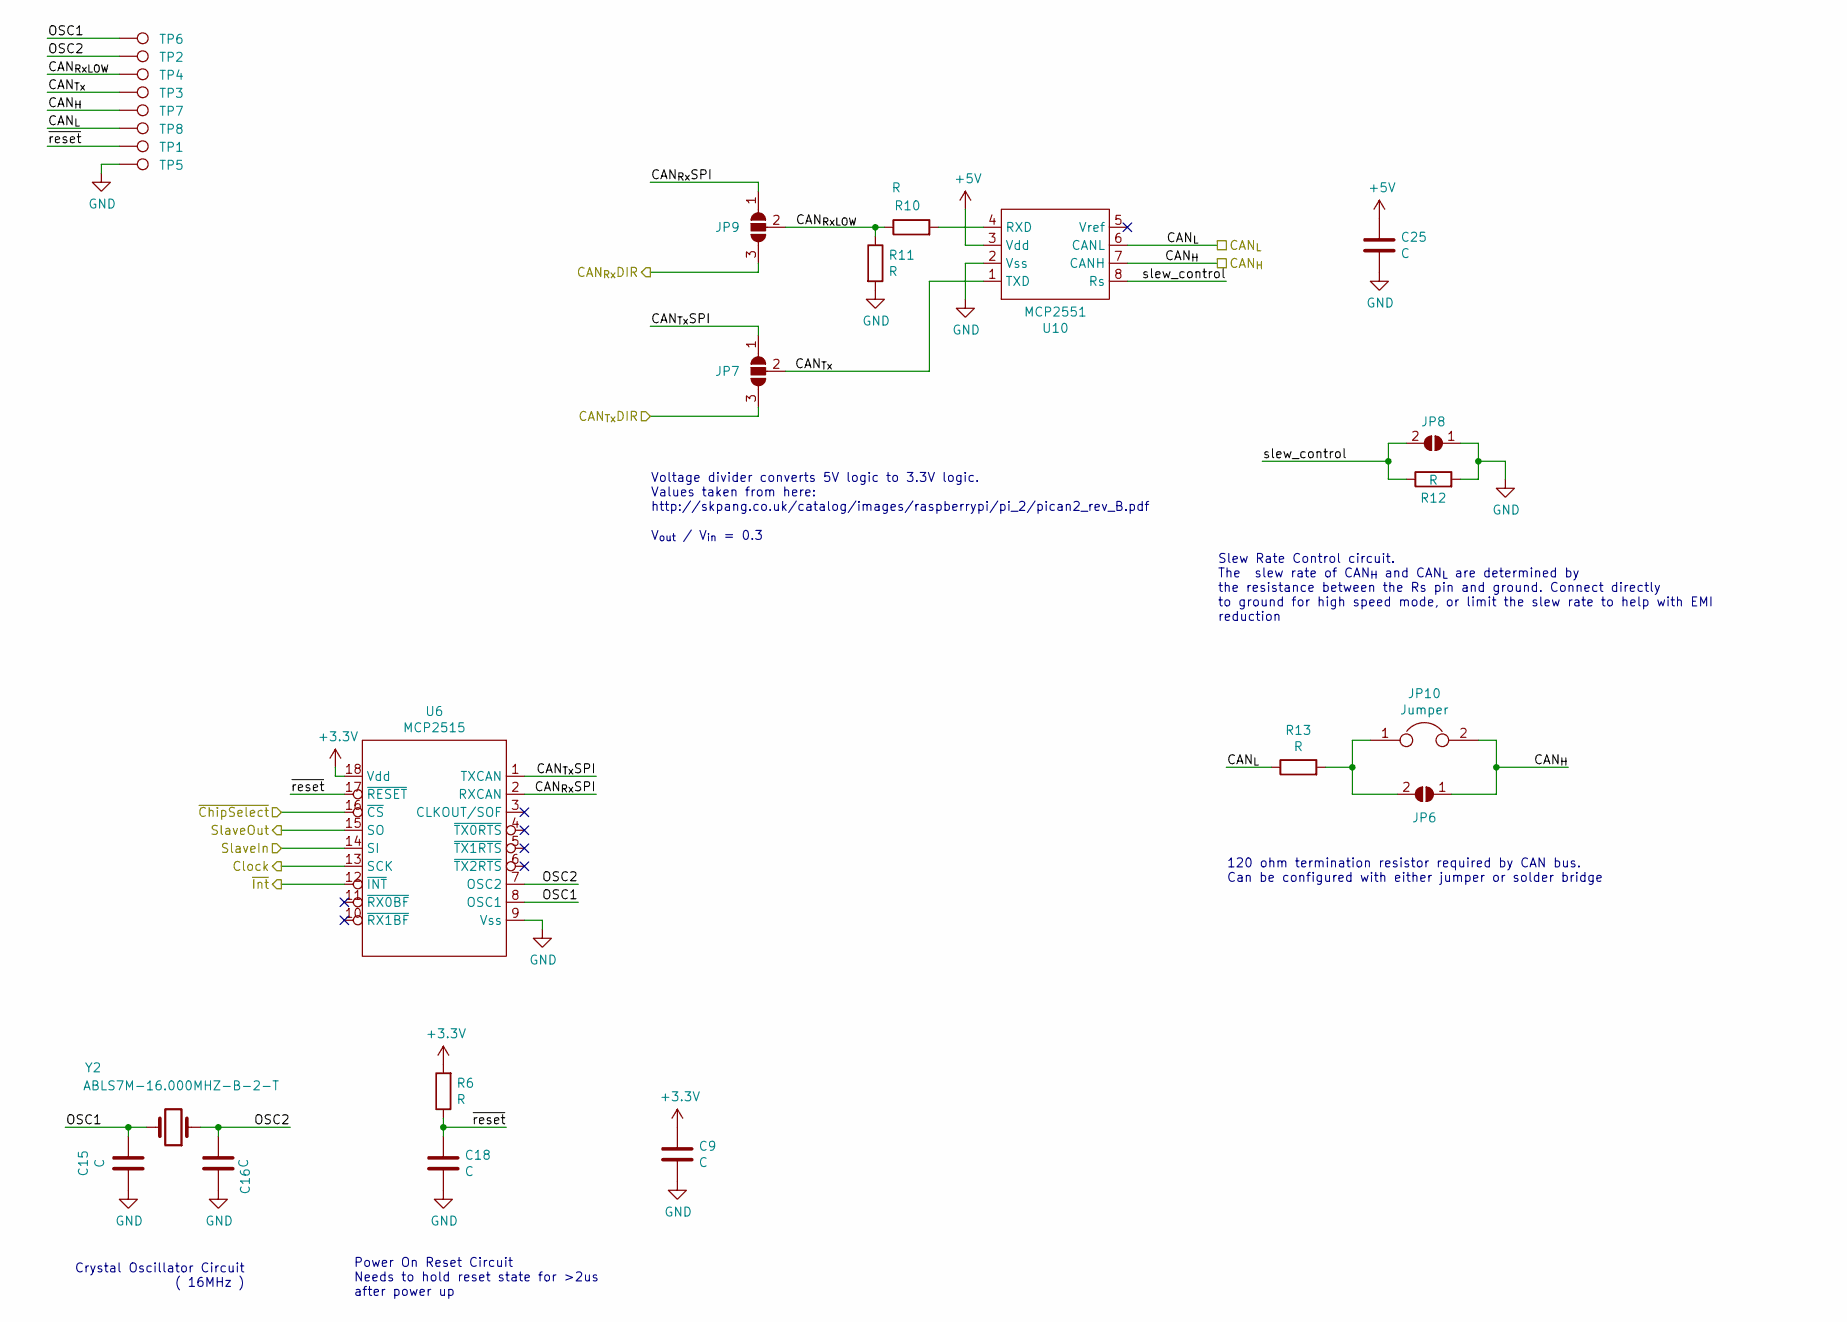
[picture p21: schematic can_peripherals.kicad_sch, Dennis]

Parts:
C9, C15, C16, C18, C25: C; C_0805_2012Metric
JP6, JP8: SolderJumper_2_Open; SolderJumper-2_P1.3mm_Open_RoundedPad1.0x1.5mm
JP7, JP9: SolderJumper_3_Open; SolderJumper-3_P1.3mm_Open_RoundedPad1.0x1.5mm_NumberLabels
JP10: Jumper; PinHeader_1x02_P2.54mm_Vertical
R6, R10, R11, R12, R13: R; R_0805_2012Metric
TP1, TP2, TP3, TP4, TP5, TP6, TP7, TP8: TestPoint; TestPoint_Pad_D1.5mm
U6: MCP2515; SOIC-18W_7.5x11.6mm_P1.27mm; Manufacturer Part MCP2515T-I/SO
U10: MCP2551; SO-8_3.9x4.9mm_P1.27mm; Manufacturer Part MCP2551T-E/SN
Y2: ABLS7M-16.000MHZ-B-2-T; Crystal-ABLS7M; Manufacturer Part ABLS7M-16.000MHZ-B-2-T

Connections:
+3V3: C9.1, R6.2, U6.18 (Vdd); also elsewhere on the board
+5V: C25.1, U10.3 (Vdd); also elsewhere on the board
/CAN Peripherals/CAN_{RxLOW}: JP9.2 (C), R10.1, R11.1, TP4.1
/CAN Peripherals/CAN_{Rx}SPI: JP9.1 (A), U6.2 (RXCAN)
/CAN Peripherals/CAN_{Tx}: JP7.2 (C), TP3.1, U10.1 (TXD)
/CAN Peripherals/CAN_{Tx}SPI: JP7.1 (A), U6.1 (TXCAN)
/CAN Peripherals/OSC1: C15.1, TP6.1, U6.8 (OSC1), Y2.2
/CAN Peripherals/OSC2: C16.1, TP2.1, U6.7 (OSC2), Y2.1
/CAN Peripherals/slew_control: JP8.2 (B), R12.1, U10.8 (Rs)
/CAN Peripherals/~reset: C18.1, R6.1, TP1.1, U6.17 (~RESET)
/CAN.RX: JP9.3 (B); also elsewhere on the board
/CAN.TX: JP7.3 (B); also elsewhere on the board
/CAN_{H}: JP6.1 (A), JP10.2, TP7.1, U10.7 (CANH); also elsewhere on the board
/CAN_{L}: R13.1, TP8.1, U10.6 (CANL); also elsewhere on the board
/SPI.CLK: U6.13 (SCK); also elsewhere on the board
/SPI.MISO: U6.15 (SO); also elsewhere on the board
/SPI.MOSI: U6.14 (SI); also elsewhere on the board
/SPI.~CS_{CAN}: U6.16 (~CS); also elsewhere on the board
/~INT_{CAN}: U6.12 (~INT); also elsewhere on the board
GND: C9.2, C15.2, C16.2, C18.2, C25.2, JP8.1 (A), R11.2, R12.2, TP5.1, U6.9 (Vss), U10.2 (Vss); also elsewhere on the board
unnamed: JP6.2 (B), JP10.1, R13.2
unnamed: R10.2, U10.4 (RXD)

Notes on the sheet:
Crystal Oscillator Circuit ( 16MHz )
Power On Reset Circuit Needs to hold reset state for >2us after power up
Voltage divider converts 5V logic to 3.3V logic. Values taken from here: http://skpang.co.uk/catalog/images/raspberrypi/pi_2/pican2_rev_B.pdf V_{out} / V_{in} = 0.3
Slew Rate Control circuit. The slew rate of CAN_{H} and CAN_{L} are determined by the resistance between the Rs pin and ground. Connect directly to ground for high speed mode, or limit the slew rate to help with EMI reduction
120 ohm termination resistor required by CAN bus. Can be configured with either jumper or solder bridge

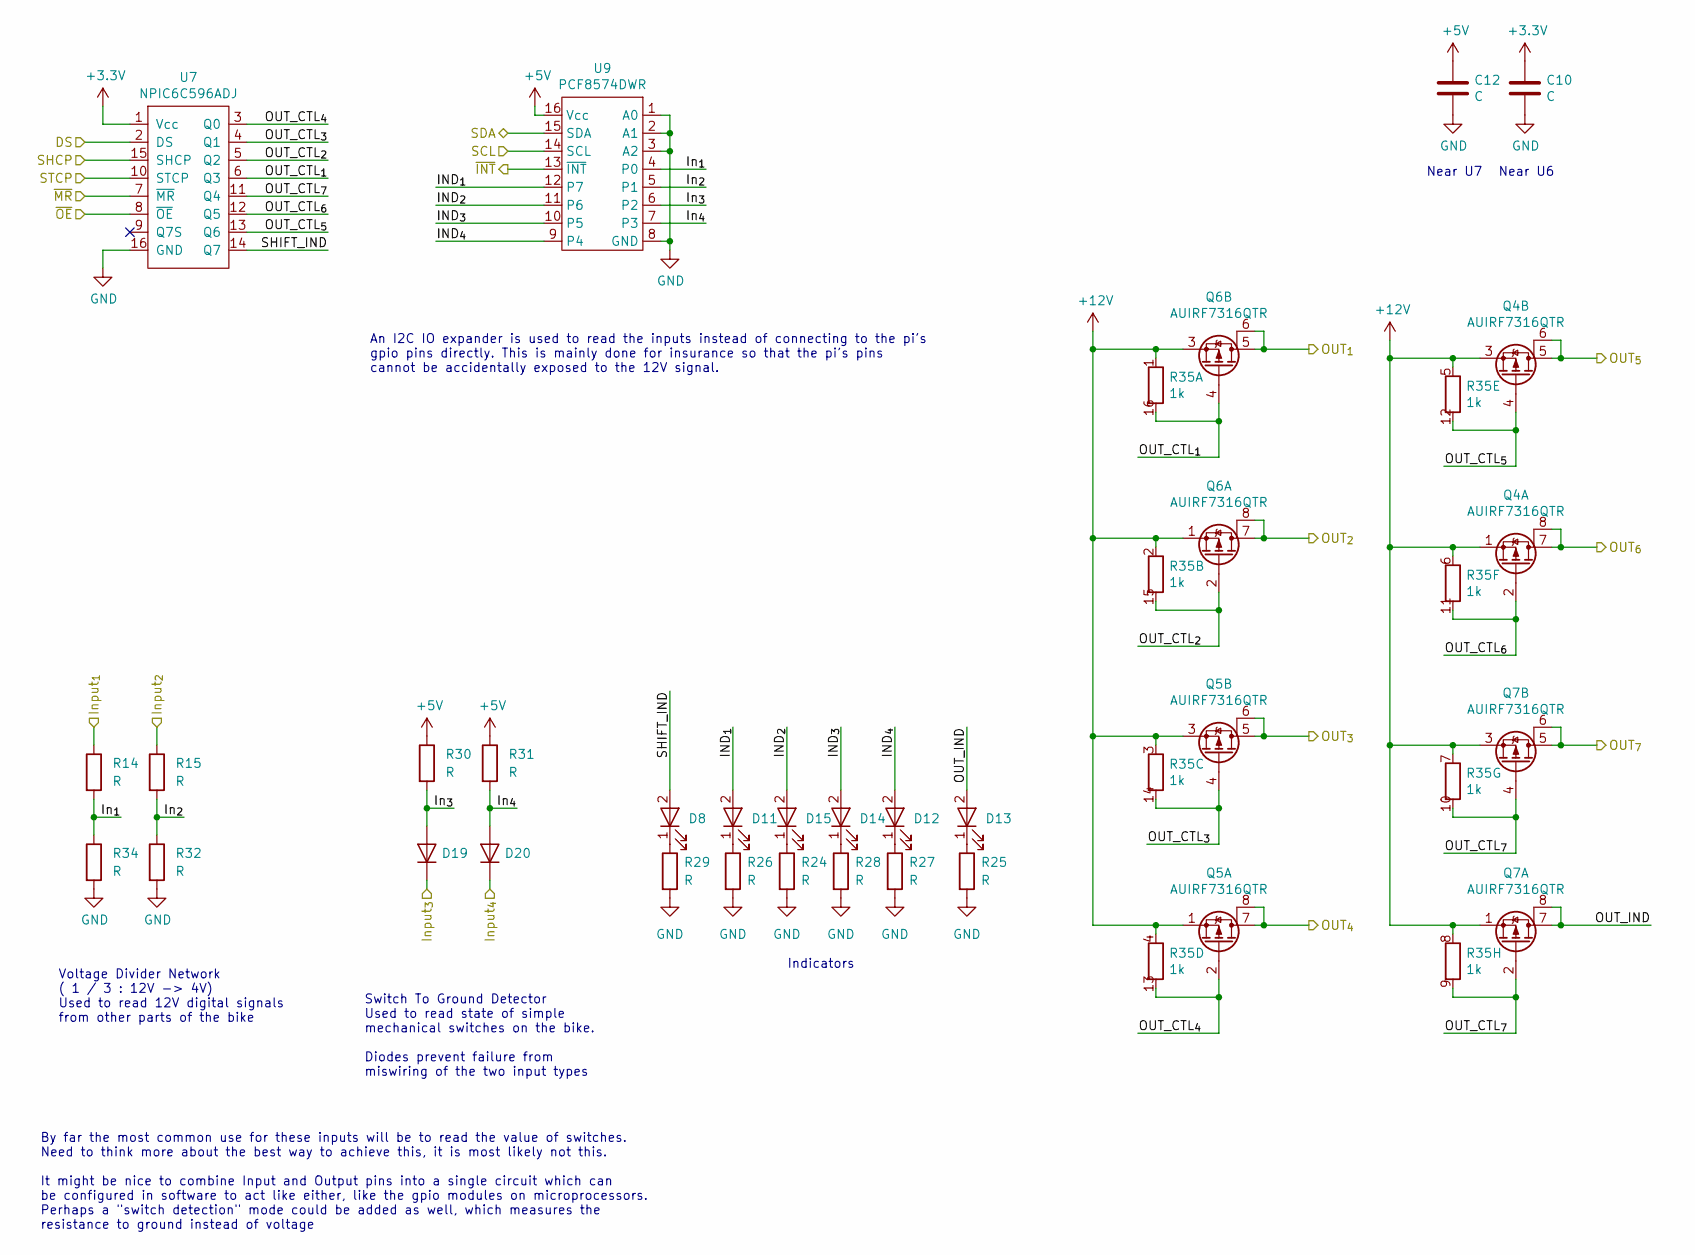
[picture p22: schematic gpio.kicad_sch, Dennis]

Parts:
C10, C12: C; C_0805_2012Metric
D8, D11, D12, D13, D14, D15: LED_Green; LED_0805_2012Metric_Pad1.15x1.40mm_HandSolder; Manufacturer Part CMD17-21VGC/TR8
D19, D20: Diode; D_SOD-123F; Manufacturer Part NHP220SFT3G
Q4, Q5, Q6, Q7: AUIRF7316QTR; SO-8_3.9x4.9mm_P1.27mm; Manufacturer Part AUIRF7316QTR
R14, R15, R24, R25, R26, R27, R28, R29, R30, R31, R32, R34: R; R_0805_2012Metric
R35: CTS-766161102GP; SOIC-16_3.9x9.9mm_P1.27mm; Manufacturer Part 766161102GP
U7: NPIC6C596ADJ; SOIC-16_4.55x10.3mm_P1.27mm; Manufacturer Part NPIC6C596ADJ
U9: PCF8574DWR; SOIC-16W_7.5x10.3mm_P1.27mm; Manufacturer Part PCF8574DWR

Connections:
+3V3: C10.1, U7.1 (Vcc); also elsewhere on the board
+5V: C12.1, R30.1, R31.1, U9.16 (Vcc); also elsewhere on the board
+12V: Q4.1 (S1), Q4.3 (S2), Q5.1 (S1), Q5.3 (S2), Q6.1 (S1), Q6.3 (S2), Q7.1 (S1), Q7.3 (S2), R35.1, R35.2, R35.3, R35.4, R35.5, R35.6, R35.7, R35.8; also elsewhere on the board
/GPIO/IND_{1}: D11.2, U9.12 (P7)
/GPIO/IND_{2}: D15.2, U9.11 (P6)
/GPIO/IND_{3}: D14.2, U9.10 (P5)
/GPIO/IND_{4}: D12.2, U9.9 (P4)
/GPIO/In_{1}: R14.2, R34.1, U9.4 (P0)
/GPIO/In_{2}: R15.2, R32.1, U9.5 (P1)
/GPIO/In_{3}: D19.2 (A), R30.2, U9.6 (P2)
/GPIO/In_{4}: D20.2 (A), R31.2, U9.7 (P3)
/GPIO/OUT_CTL_{1}: Q6.4 (G2), R35.16, U7.6 (Q3)
/GPIO/OUT_CTL_{2}: Q6.2 (G1), R35.15, U7.5 (Q2)
/GPIO/OUT_CTL_{3}: Q5.4 (G2), R35.14, U7.4 (Q1)
/GPIO/OUT_CTL_{4}: Q5.2 (G1), R35.13, U7.3 (Q0)
/GPIO/OUT_CTL_{5}: Q4.4 (G2), R35.12, U7.13 (Q6)
/GPIO/OUT_CTL_{6}: Q4.2 (G1), R35.11, U7.12 (Q5)
/GPIO/OUT_CTL_{7}: Q7.2 (G1), Q7.4 (G2), R35.9, R35.10, U7.11 (Q4)
/GPIO/OUT_IND: D13.2, Q7.7 (D1), Q7.8 (D1)
/GPIO/SHIFT_IND: D8.2, U7.14 (Q7)
/GPIO_{DATA}: U7.2 (DS); also elsewhere on the board
/GPIO_{rCLK}: U7.10 (STCP); also elsewhere on the board
/GPIO_{sCLK}: U7.15 (SHCP); also elsewhere on the board
/Input_{1}: R14.1; also elsewhere on the board
/Input_{2}: R15.1; also elsewhere on the board
/Input_{3}: D19.1 (K); also elsewhere on the board
/Input_{4}: D20.1 (K); also elsewhere on the board
/Output_{1}: Q6.5 (D2), Q6.6 (D2); also elsewhere on the board
/Output_{2}: Q6.7 (D1), Q6.8 (D1); also elsewhere on the board
/Output_{3}: Q5.5 (D2), Q5.6 (D2); also elsewhere on the board
/Output_{4}: Q5.7 (D1), Q5.8 (D1); also elsewhere on the board
/Output_{5}: Q4.5 (D2), Q4.6 (D2); also elsewhere on the board
/Output_{6}: Q4.7 (D1), Q4.8 (D1); also elsewhere on the board
/Output_{7}: Q7.5 (D2), Q7.6 (D2); also elsewhere on the board
/SCL_{5V}: U9.14 (SCL); also elsewhere on the board
/SDA_{5V}: U9.15 (SDA); also elsewhere on the board
/~GPIO_{OE}: U7.8 (~OE); also elsewhere on the board
/~GPIO_{RS}: U7.7 (~MR); also elsewhere on the board
/~INT_{GPIO}: U9.13 (~INT); also elsewhere on the board
GND: C10.2, C12.2, R24.2, R25.2, R26.2, R27.2, R28.2, R29.2, R32.2, R34.2, U7.16 (GND), U9.1 (A0), U9.2 (A1), U9.3 (A2), U9.8 (GND); also elsewhere on the board
unnamed: D8.1, R29.1
unnamed: D11.1, R26.1
unnamed: D12.1, R27.1
unnamed: D13.1, R25.1
unnamed: D14.1, R28.1
unnamed: D15.1, R24.1

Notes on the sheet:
By far the most common use for these inputs will be to read the value of switches. Need to think more about the best way to achieve this, it is most likely not this. It might be nice to combine Input and Output pins into a single circuit which can be configured in software to act like either, like 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
Voltage Divider Network ( 1 / 3 : 12V -> 4V) Used to read 12V digital signals from other parts of the bike
Switch To Ground Detector Used to read state of simple mechanical switches on the bike. Diodes prevent failure from miswiring of the two input types
An I2C IO expander is used to read the inputs instead of connecting to the pi's gpio pins directly. This is mainly done for insurance so that the pi's pins cannot be accidentally exposed to the 12V signal.
Indicators
Near U7
Near U6

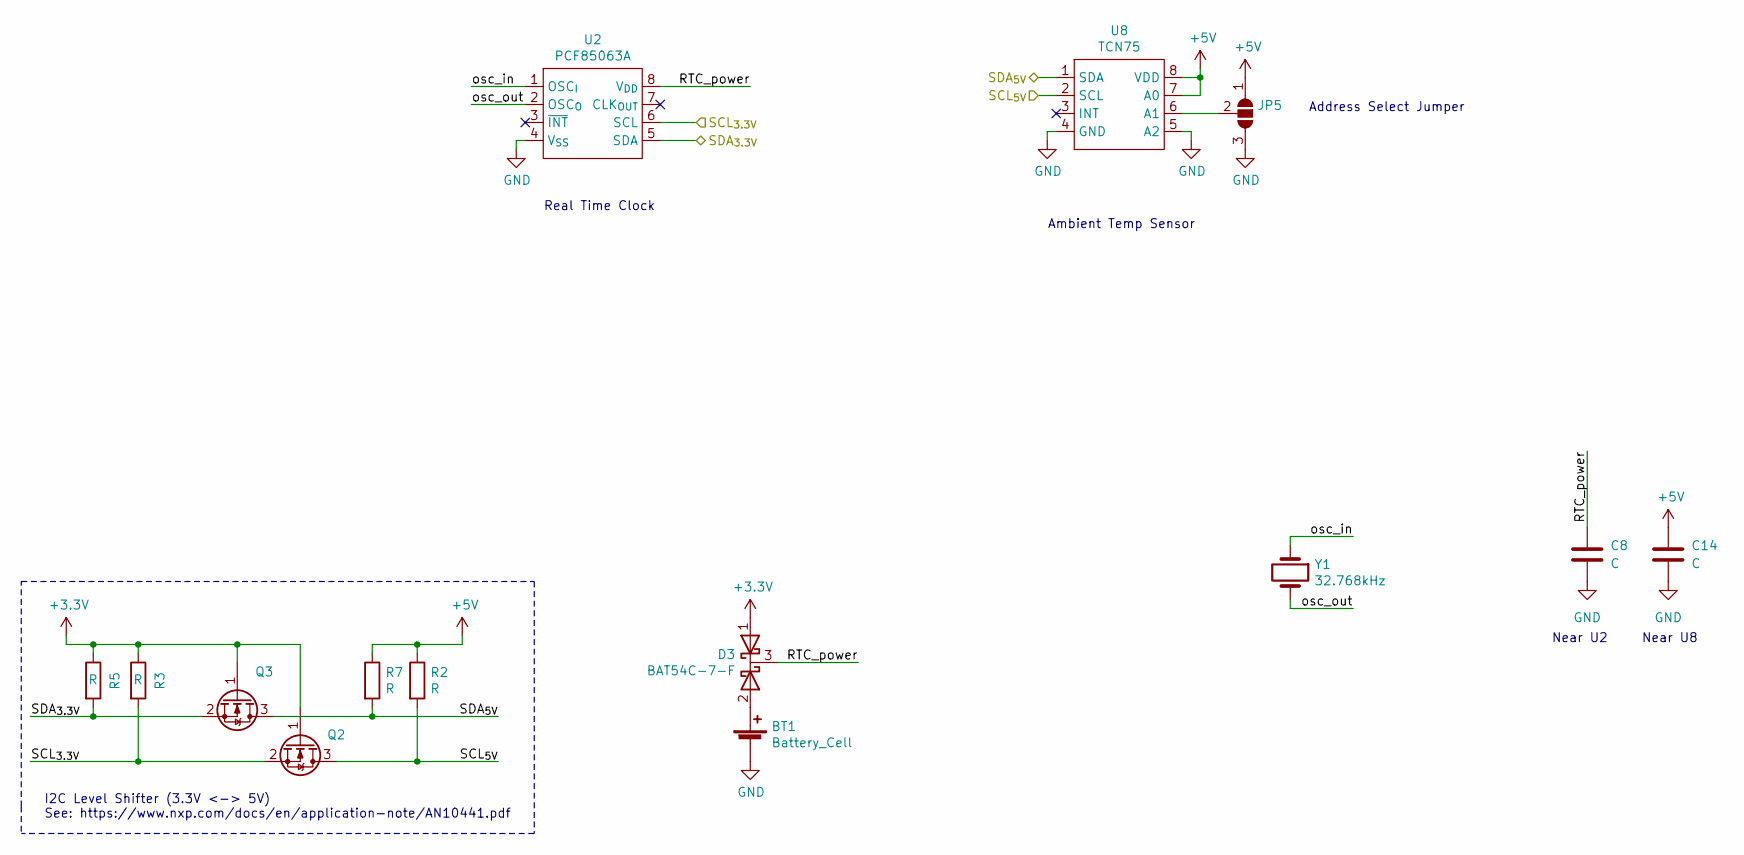
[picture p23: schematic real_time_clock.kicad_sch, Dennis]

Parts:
BT1: Battery_Cell; BatteryHolder_Keystone_3001_1x12mm; Manufacturer Part 3001
C8, C14: C; C_0805_2012Metric
D3: BAT54C-7-F; SOT-23; Manufacturer Part BAT54C-7-F
JP5: SolderJumper_3_Open; SolderJumper-3_P1.3mm_Open_RoundedPad1.0x1.5mm_NumberLabels
Q2, Q3: DMN62D0U-7; SOT-23; Manufacturer Part DMN62D0U-7
R2, R3, R5, R7: R; R_0805_2012Metric
U2: PCF85063A; SOIC-8_3.9x4.9mm_P1.27mm; Manufacturer Part PCF85063AT/AY
U8: TCN75; SOIC-8_3.9x4.9mm_P1.27mm; Supply Voltage 5.0V; Manufacturer Part TCN75-5.0MOA
Y1: Crystal-CM7V-T1A-32.768kHz; Crystal-CM7V; Manufacturer Part CM7V-T1A-32.768KHZ-6PF-20PPM-TB-QA

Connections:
+3V3: D3.1 (Anode_{1}), Q2.1 (G), Q3.1 (G), R3.1, R5.1; also elsewhere on the board
+5V: C14.1, JP5.1 (A), R2.1, R7.1, U8.7 (A0), U8.8 (VDD); also elsewhere on the board
/I2C extras/RTC_power: C8.1, D3.3 (Cathode), U2.8 (V_{DD})
/I2C extras/osc_in: U2.1 (OSC_{I}), Y1.1
/I2C extras/osc_out: U2.2 (OSC_{O}), Y1.2
/SCL_{3.3V}: Q2.2 (S), R3.2, U2.6 (SCL); also elsewhere on the board
/SCL_{5V}: Q2.3 (D), R2.2, U8.2 (SCL); also elsewhere on the board
/SDA_{3.3V}: Q3.2 (S), R5.2, U2.5 (SDA); also elsewhere on the board
/SDA_{5V}: Q3.3 (D), R7.2, U8.1 (SDA); also elsewhere on the board
GND: BT1.2 (-), C8.2, C14.2, JP5.3 (B), U2.4 (V_{SS}), U8.4 (GND), U8.5 (A2); also elsewhere on the board
unnamed: BT1.1 (+), D3.2 (Anode_{2})
unnamed: JP5.2 (C), U8.6 (A1)

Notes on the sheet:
I2C Level Shifter (3.3V <-> 5V) See: https://www.nxp.com/docs/en/application-note/AN10441.pdf
Real Time Clock
Ambient Temp Sensor
Address Select Jumper
Near U2
Near U8

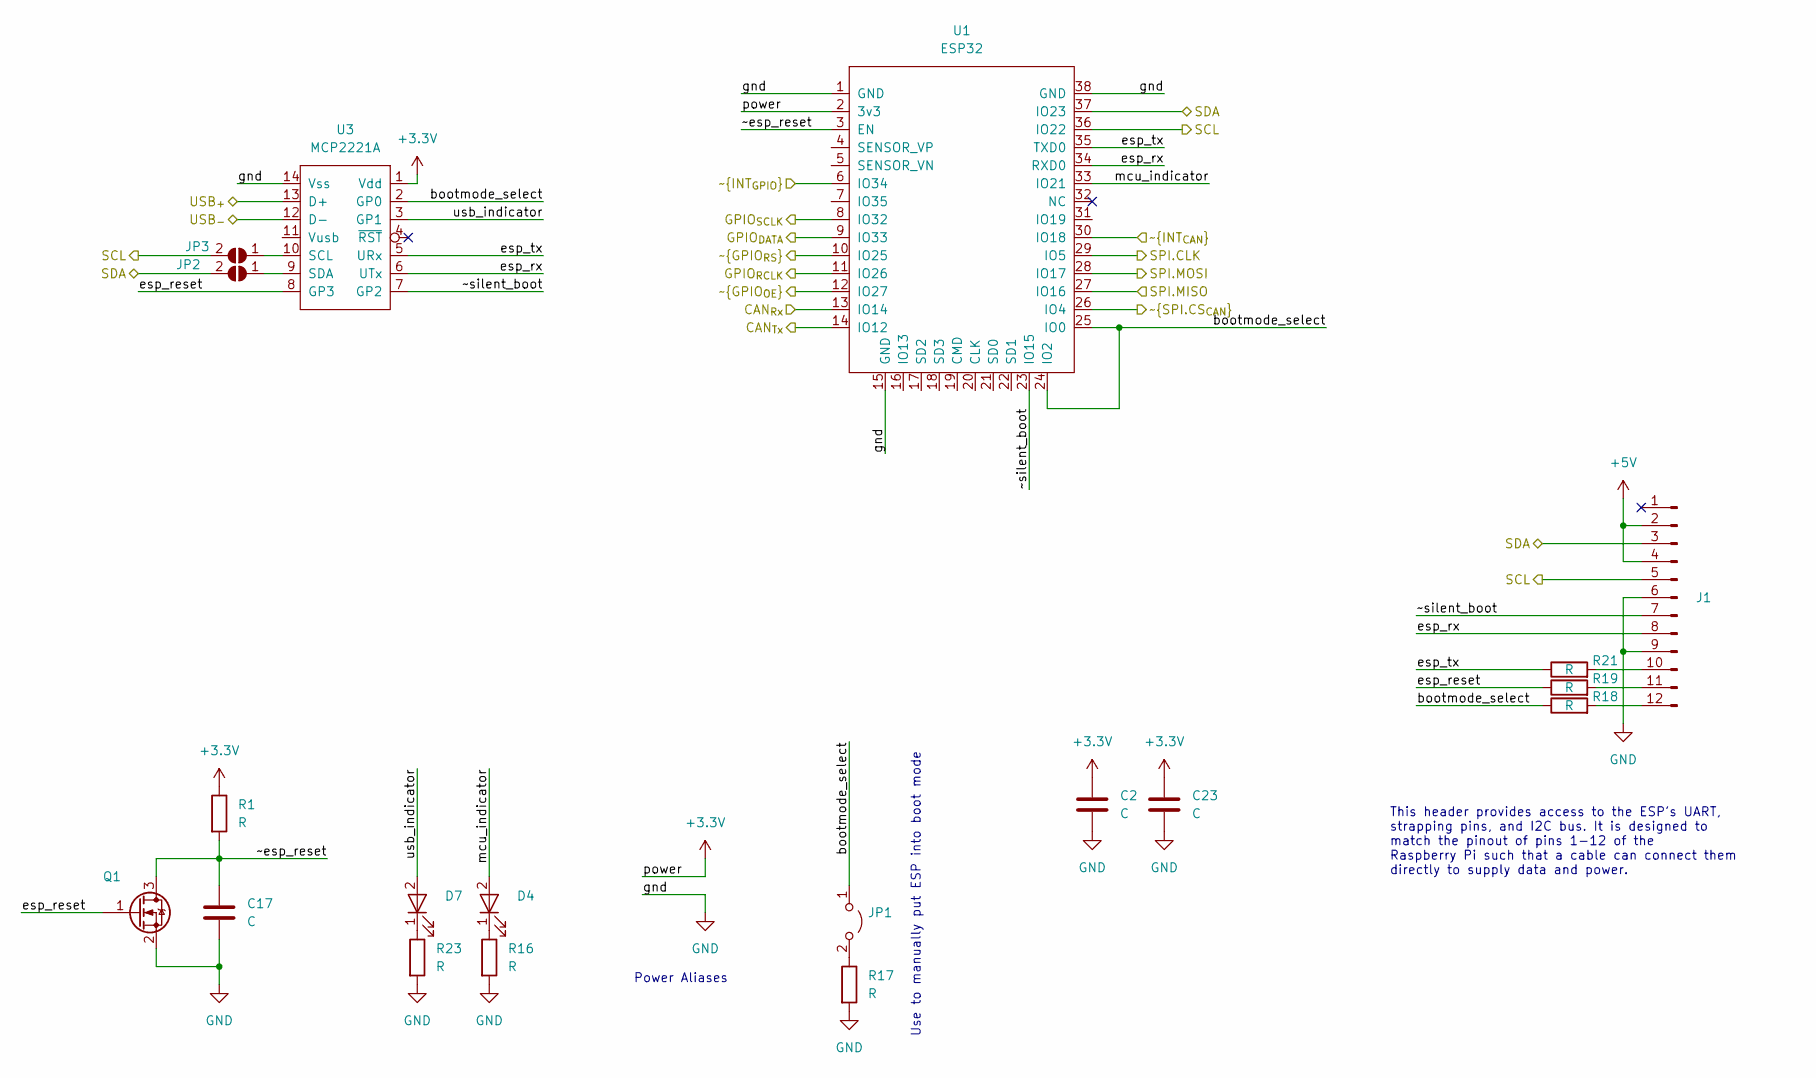
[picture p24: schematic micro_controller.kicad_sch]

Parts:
C2, C17, C23: C; C_0805_2012Metric
D4, D7: LED_Green; LED_0805_2012Metric_Pad1.15x1.40mm_HandSolder; Manufacturer Part CMD17-21VGC/TR8
J1: Conn_01x12_Male; PinHeader_2x06_P2.54mm_Vertical
JP1: Jumper_2_Open; PinHeader_1x02_P2.54mm_Vertical
JP2, JP3: SolderJumper_2_Open; SolderJumper-2_P1.3mm_Open_RoundedPad1.0x1.5mm
Q1: DMN62D0U-7; SOT-23; Manufacturer Part DMN62D0U-7
R1, R16, R17, R18, R19, R21, R23: R; R_0805_2012Metric
U1: ESP32; MODULE_ESP32-WROOM-32; Manufacturer Part ESP32-WROOM-32
U3: MCP2221A; TSSOP-14_4.4x5mm_P0.65mm; Manufacturer Part MCP2221AT-I/ST

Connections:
+3V3: C2.1, C23.1, R1.1, U1.2 (3v3), U3.1 (Vdd); also elsewhere on the board
+5V: J1.2, J1.4; also elsewhere on the board
/CAN.RX: U1.13 (IO14); also elsewhere on the board
/CAN.TX: U1.14 (IO12); also elsewhere on the board
/GPIO_{DATA}: U1.9 (IO33); also elsewhere on the board
/GPIO_{rCLK}: U1.11 (IO26); also elsewhere on the board
/GPIO_{sCLK}: U1.8 (IO32); also elsewhere on the board
/MicroController/bootmode_select: JP1.1 (A), R18.1, U1.24 (IO2), U1.25 (IO0), U3.2 (GP0)
/MicroController/esp_reset: Q1.1 (G), R19.1, U3.8 (GP3)
/MicroController/esp_rx: J1.8, U1.34 (RXD0), U3.6 (UTx)
/MicroController/esp_tx: R21.1, U1.35 (TXD0), U3.5 (URx)
/MicroController/mcu_indicator: D4.2, U1.33 (IO21)
/MicroController/usb_indicator: D7.2, U3.3 (GP1)
/MicroController/~esp_reset: C17.1, Q1.3 (D), R1.2, U1.3 (EN)
/MicroController/~silent_boot: J1.7, U1.23 (IO15), U3.7 (GP2)
/SCL_{3.3V}: J1.5, JP3.2 (B), U1.36 (IO22); also elsewhere on the board
/SDA_{3.3V}: J1.3, JP2.2 (B), U1.37 (IO23); also elsewhere on the board
/SPI.CLK: U1.29 (IO5); also elsewhere on the board
/SPI.MISO: U1.27 (IO16); also elsewhere on the board
/SPI.MOSI: U1.28 (IO17); also elsewhere on the board
/SPI.~CS_{CAN}: U1.26 (IO4); also elsewhere on the board
/USB.+: U3.13 (D+); also elsewhere on the board
/USB.-: U3.12 (D-); also elsewhere on the board
/~GPIO_{OE}: U1.12 (IO27); also elsewhere on the board
/~GPIO_{RS}: U1.10 (IO25); also elsewhere on the board
/~INT_{CAN}: U1.30 (IO18); also elsewhere on the board
/~INT_{GPIO}: U1.6 (IO34); also elsewhere on the board
GND: C2.2, C17.2, C23.2, J1.6, J1.9, Q1.2 (S), R16.2, R17.2, R23.2, U1.1 (GND), U1.15 (GND), U1.38 (GND), U3.14 (Vss); also elsewhere on the board
unnamed: D4.1, R16.1
unnamed: D7.1, R23.1
unnamed: J1.10, R21.2
unnamed: J1.11, R19.2
unnamed: J1.12, R18.2
unnamed: JP1.2 (B), R17.1
unnamed: JP2.1 (A), U3.9 (SDA)
unnamed: JP3.1 (A), U3.10 (SCL)

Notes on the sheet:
Power Aliases
Use to manually put ESP into boot mode
This header provides access to the ESP's UART, strapping pins, and I2C bus. It is designed to match the pinout of pins 1-12 of the Raspberry Pi such that a cable can connect them directly to supply data and power.

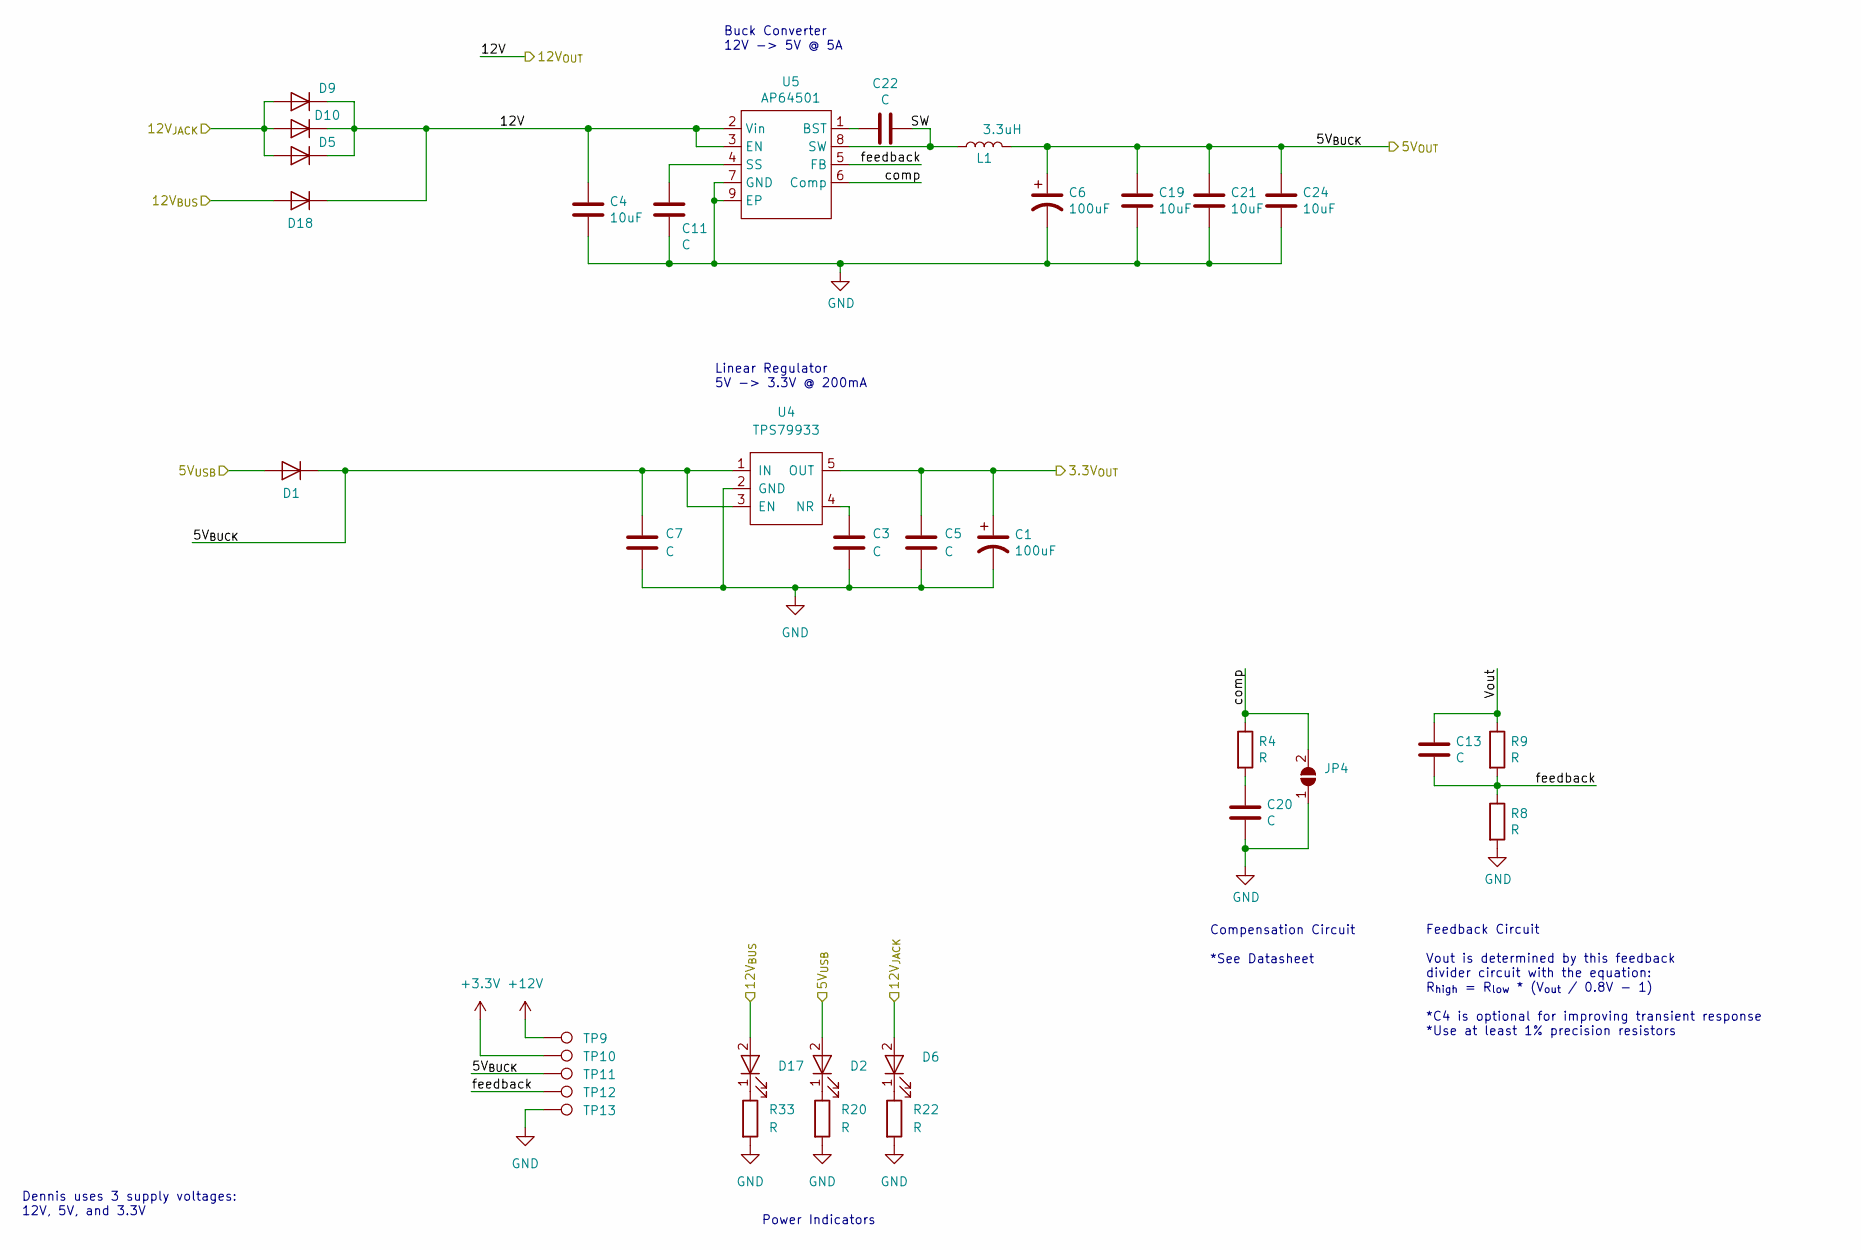
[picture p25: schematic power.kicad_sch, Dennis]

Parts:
C1, C6: 100uF; CP_Elec_6.3x5.9; Voltage 25V; Manufacturer Part A768EB107M1ELAS036
C3, C5, C7, C11, C13, C20, C22: C; C_0805_2012Metric
C4, C19, C21, C24: 10uF; C_0805_2012Metric; Voltage Rating 16V; Tolerance 20%; Manufacturer Part C2012X5R1C106K085AC
D1, D5, D9, D10, D18: Diode; D_SOD-123F; Manufacturer Part NHP220SFT3G
D2, D6, D17: LED_Green; LED_0805_2012Metric_Pad1.15x1.40mm_HandSolder; Manufacturer Part CMD17-21VGC/TR8
JP4: SolderJumper_2_Open; SolderJumper-2_P1.3mm_Open_RoundedPad1.0x1.5mm
L1: 3.3uH; Bourns SRN6045Y Inductor; Manufacturer Part SRN6045TA-3R3Y
R4, R8, R9, R20, R22, R33: R; R_0805_2012Metric
TP9, TP10, TP11, TP12, TP13: TestPoint; TestPoint_Pad_D1.5mm
U4: TPS79933; SOT-23-5; Manufacturer Part TPS79933DDCR
U5: AP64501; SOIC-8-1EP_3.9x4.9mm_P1.27mm_EP2.514x3.2mm; Manufacturer Part AP64501SP-13

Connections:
+3V3: C1.1, C5.1, TP10.1, U4.5 (OUT); also elsewhere on the board
+5V: C6.1, C7.1, C19.1, C21.1, C24.1, D1.1 (K), L1.2, TP11.1, U4.1 (IN), U4.3 (EN); also elsewhere on the board
+12V: C4.1, D5.1 (K), D9.1 (K), D10.1 (K), D18.1 (K), TP9.1, U5.2 (Vin), U5.3 (EN); also elsewhere on the board
/BUS.PWR_{IN}: D17.2, D18.2 (A); also elsewhere on the board
/Jack_PWR: D5.2 (A), D6.2, D9.2 (A), D10.2 (A); also elsewhere on the board
/Power Supply/SW: C22.2, L1.1, U5.8 (SW)
/Power Supply/Vout: C13.1, R9.1
/Power Supply/comp: JP4.2 (B), R4.1, U5.6 (Comp)
/Power Supply/feedback: C13.2, R8.1, R9.2, TP12.1, U5.5 (FB)
/USB.PWR: D1.2 (A), D2.2; also elsewhere on the board
GND: C1.2, C3.2, C4.2, C5.2, C6.2, C7.2, C11.2, C19.2, C20.2, C21.2, C24.2, JP4.1 (A), R8.2, R20.2, R22.2, R33.2, TP13.1, U4.2 (GND), U5.7 (GND), U5.9 (EP); also elsewhere on the board
unnamed: C3.1, U4.4 (NR)
unnamed: C11.1, U5.4 (SS)
unnamed: C20.1, R4.2
unnamed: C22.1, U5.1 (BST)
unnamed: D2.1, R20.1
unnamed: D6.1, R22.1
unnamed: D17.1, R33.1

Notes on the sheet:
Dennis uses 3 supply voltages: 12V, 5V, and 3.3V
Linear Regulator 5V -> 3.3V @ 200mA
Buck Converter 12V -> 5V @ 5A
Power Indicators
Compensation Circuit *See Datasheet
Feedback Circuit Vout is determined by this feedback divider circuit with the equation: R_{high} = R_{low} * (V_{out} / 0.8V - 1) *C4 is optional for improving transient response *Use at least 1% precision resistors

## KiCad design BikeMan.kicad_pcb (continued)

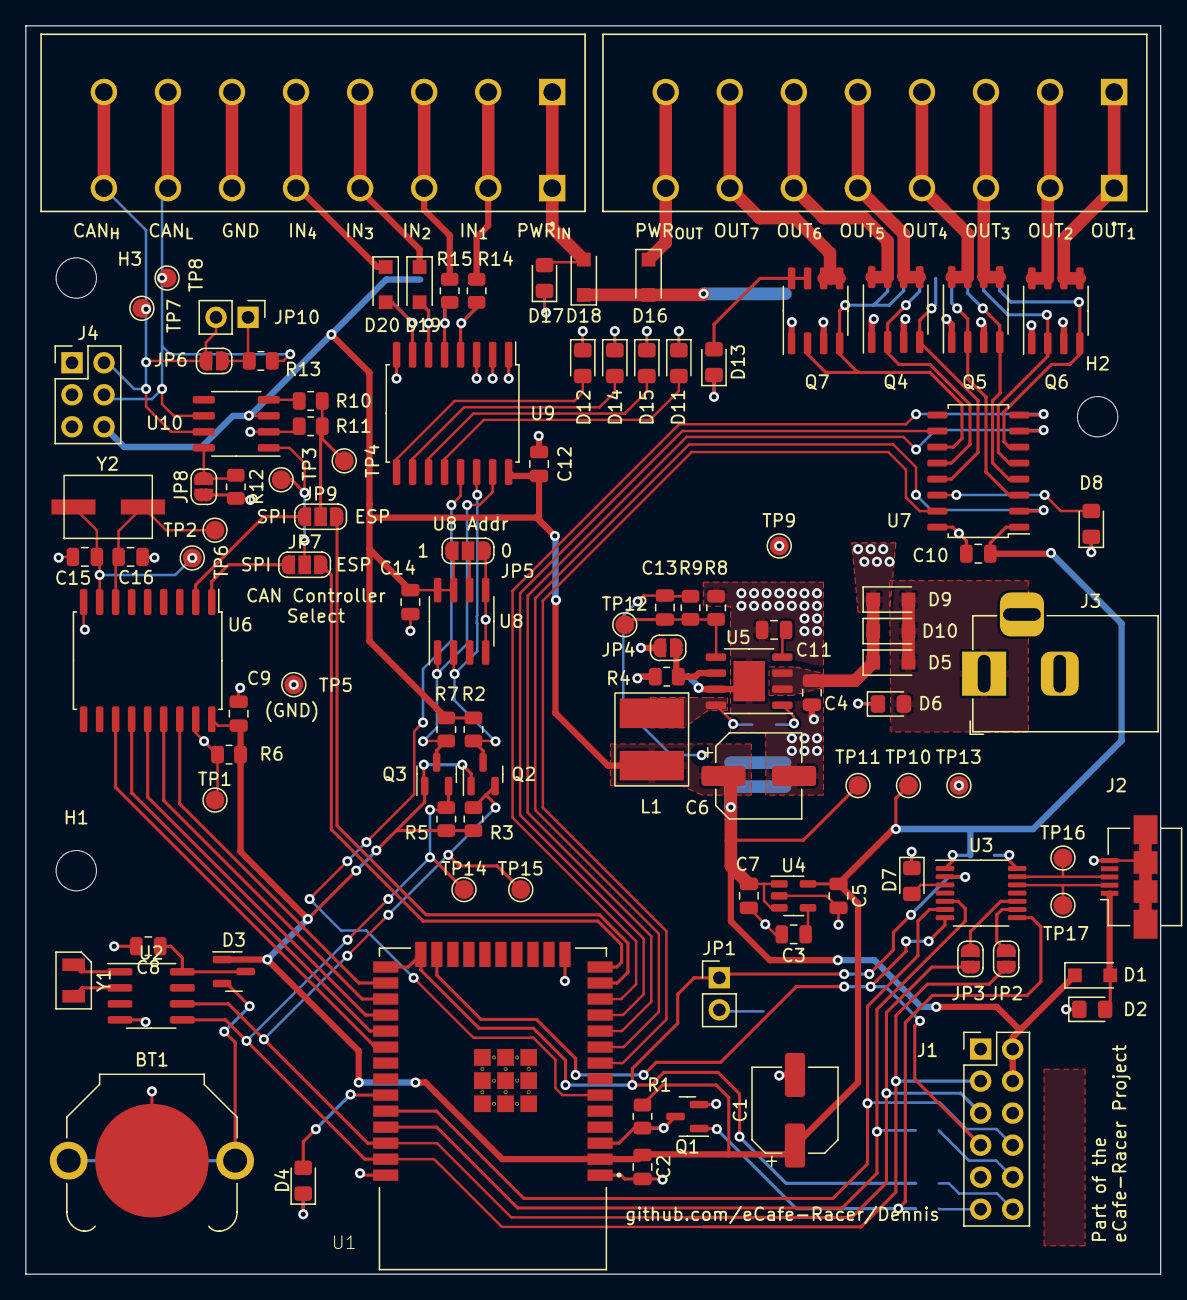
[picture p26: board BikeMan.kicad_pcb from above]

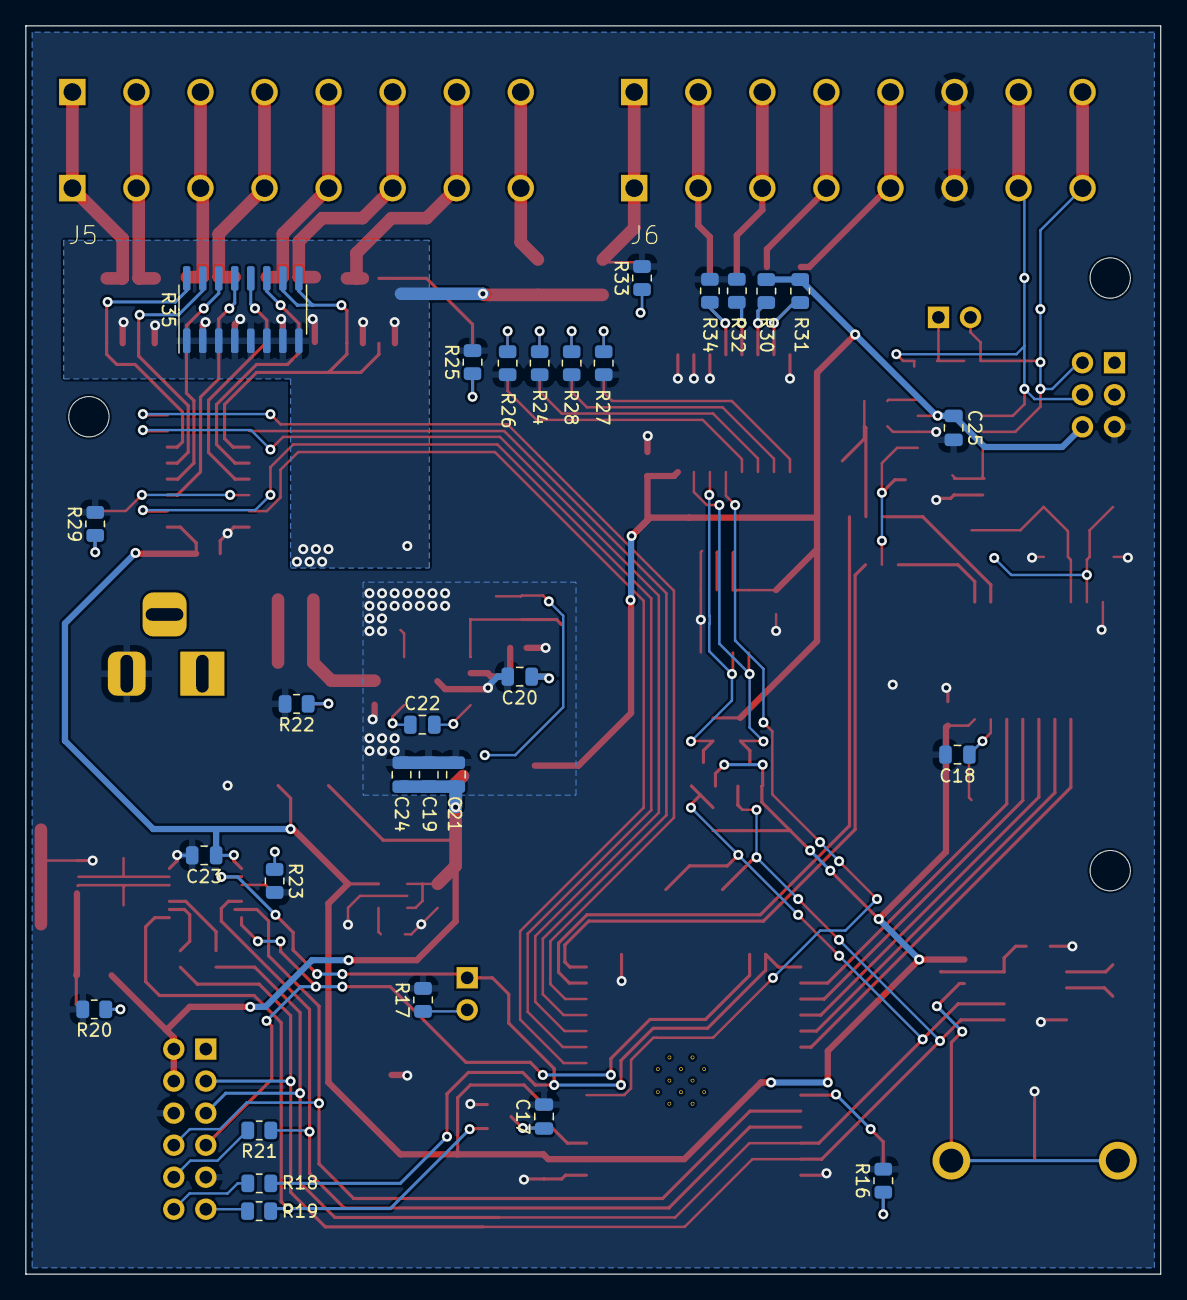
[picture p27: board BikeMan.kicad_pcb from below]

Board: 2 copper layers, 90.0 x 99.0 mm, 137 parts (29 on the bottom side), 105 nets.

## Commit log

2020-11-28 created project
    [BikeMan.kicad_pcb, BikeMan.sch]
2020-12-18 Migrated to KiCad 6.0
    [BikeMan.kicad_sch, can_peripherals.kicad_sch, compute_module.kicad_sch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]
2020-12-29 Added 12V GPIO module
    [BikeMan.kicad_sch, gpio.kicad_sch]
2020-12-29 Added LC values and inductor part number to buck converter circuit
    [power.kicad_sch]
2020-12-29 Added annotated reference numbers
    [can_peripherals.kicad_sch, compute_module.kicad_sch]
2020-12-29 Finished CAN peripheral
    [BikeMan.kicad_sch, can_peripherals.kicad_sch]
2020-12-31 Real Time Clock circuit
    [real_time_clock.kicad_sch]
2020-12-31 added HDMI connector
    [compute_module_B.kicad_sch]
2020-12-31 Changes to top level schematic
    [BikeMan.kicad_sch]
2020-12-31 Added USB hub IC
    [compute_module_B.kicad_sch]
2020-12-31 Deleted leftover files from old file format
    [BikeMan.sch]
2020-12-31 visual tweaks to schematic
    [BikeMan.kicad_sch, can_peripherals.kicad_sch, compute_module.kicad_sch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]
2020-12-31 cleaning up workspace
    [BikeMan.kicad_sch, can_peripherals.kicad_sch, compute_module_A.kicad_sch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]
2020-12-31 default BOM config file
2020-12-31 Messed with the schematic page border
2020-12-31 Added buses and USB ports to schematic
    [BikeMan.kicad_sch, can_peripherals.kicad_sch, compute_module_A.kicad_sch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]
2020-12-31 Plotted Schematic for v0.1.1
2021-01-19 Added connector for ethernet
    [compute_module_A.kicad_sch, compute_module_B.kicad_sch]
2021-01-20 SD card circuits
    [BikeMan.kicad_sch, can_peripherals.kicad_sch, compute_module_A.kicad_sch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]
2021-01-21 starting layout
    [BikeMan.kicad_pcb]
2021-01-22 Adding footprints and step files for connectors
    [BikeMan.kicad_pcb, BikeMan.kicad_sch, can_peripherals.kicad_sch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]
2021-02-04 footprint assignments
    [BikeMan.kicad_pcb, BikeMan.kicad_sch, can_peripherals.kicad_sch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]
2021-02-05 WIP 5 FEB 2021
    [BikeMan.kicad_pcb, BikeMan.kicad_sch, gpio.kicad_sch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]
2021-02-18 switched to networked resistors on GPIO system
    [BikeMan.kicad_pcb, BikeMan.kicad_sch, can_peripherals.kicad_sch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]
2021-02-26 Added Daughter Card
    [BikeMan.kicad_pcb, BikeMan.kicad_sch, can_peripherals.kicad_sch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]
2021-03-02 more layout: power supply and gpio
    [BikeMan.kicad_pcb, BikeMan.kicad_sch, can_peripherals.kicad_sch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]
2021-03-20 Routing for HDMI, Ethernet, SD Card, CAN
    [BikeMan.kicad_pcb, BikeMan.kicad_sch, can_peripherals.kicad_sch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]
2021-03-22 Finished trace routing
    [BikeMan.kicad_pcb, BikeMan.kicad_sch, can_peripherals.kicad_sch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]
2021-03-30 Cleaning up
    Reassigned reference designators to better match their position on the board.
    Moved USB hub IC and related circuits to their own sheet in the schematic.
    Tweaked reference designator positions on board to improve visibility.
    [BikeMan.kicad_pcb, BikeMan.kicad_sch, can_peripherals.kicad_sch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]
2021-03-30 Documentation for v0.1.3
    Plotted schematic and generated images of board from several angles
2021-08-03 migrated computers
    [BikeMan.kicad_sch, can_peripherals.kicad_sch, compute_module_A.kicad_sch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]
2021-08-03 removed Compute Module
    [BikeMan.kicad_sch, compute_module_A.kicad_sch, compute_module_B.kicad_sch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]
2021-08-03 tweaked CAN interface
    [can_peripherals.kicad_sch]
2021-08-03 started cleaning layout
    [BikeMan.kicad_pcb]
2021-08-04 layout sketching
    [BikeMan.kicad_pcb, BikeMan.kicad_sch, can_peripherals.kicad_sch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]
2021-08-05 components group and placed in roughly the right position
    [BikeMan.kicad_pcb, BikeMan.kicad_sch, gpio.kicad_sch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]
2021-08-06 finished routing
    [BikeMan.kicad_pcb, BikeMan.kicad_sch, can_peripherals.kicad_sch]
2021-08-06 geographical reannotate
    [BikeMan.kicad_pcb, BikeMan.kicad_sch, can_peripherals.kicad_sch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]
2021-08-06 added test points and cleaned up silk screen
    [BikeMan.kicad_pcb, BikeMan.kicad_sch, power.kicad_sch]
2021-08-06 updated 3d models
    [BikeMan.kicad_pcb, BikeMan.kicad_sch]
2021-08-07 cleaned up schematic
    [BikeMan.kicad_pcb, BikeMan.kicad_sch, can_peripherals.kicad_sch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]
2021-08-07 Forgot to connect the interrupt signal for the GPIO
    [BikeMan.kicad_pcb, BikeMan.kicad_sch, can_peripherals.kicad_sch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]
2021-08-08 gerbers for 0.2
    [BikeMan-B_Cu.gbr, BikeMan-B_Mask.gbr, BikeMan-B_Paste.gbr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]
